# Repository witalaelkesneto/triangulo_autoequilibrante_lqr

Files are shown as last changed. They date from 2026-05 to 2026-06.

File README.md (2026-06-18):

# Triângulo Autoequilibrante com Roda de Reação

Este repositório reúne os códigos, modelos 3D e arquivos auxiliares desenvolvidos para o projeto **Desenvolvimento de um Triângulo Autoequilibrante como Plataforma Didática de Controle**, elaborado como parte do trabalho de conclusão do curso de Engenharia de Controle e Automação.

O projeto consiste no desenvolvimento de uma planta didática baseada em um triângulo autoequilibrante com roda de reação. A proposta tem como objetivo integrar conceitos de modelagem matemática, controle moderno, controle não linear, sistemas embarcados, instrumentação e validação experimental em uma plataforma física de baixo custo.

A planta utiliza uma estrutura fabricada por impressão 3D, um motor de corrente contínua com encoder integrado, um sensor inercial MPU6050, uma roda de reação e um microcontrolador ESP32. O controle é dividido em duas etapas principais: uma estratégia de elevação automática do tipo *swing-up*, baseada no princípio de controle de energia, e um controlador LQR discreto responsável pela estabilização da planta em torno da posição vertical.

## Vídeo do projeto

O vídeo demonstrativo do funcionamento da planta pode ser acessado no link abaixo:

- **Vídeo:** https://youtu.be/2tPs7unF_Ww

## Estrutura do repositório

O repositório contém os principais arquivos utilizados nas etapas de modelagem, simulação, implementação embarcada, coleta de dados, geração dos gráficos experimentais e fabricação da estrutura mecânica.

```text
.
├── Modelo 3D
│   ├── STEP
│   │   ├── CAD Imports
│   │   ├── Assembly 1.step
│   │   ├── Suporte.step
│   │   ├── Triangle_Frame.step
│   │   ├── Triangle_ESP.step
│   │   ├── cubli_motor_holder_3x.step
│   │   └── reaction_wheel.step
│   │
│   └── STL
│       ├── CAD Imports
│       ├── Assembly 1.stl
│       ├── Suporte.stl
│       ├── Triangle_Frame.stl
│       ├── Triangle_ESP.stl
│       ├── cubli_motor_holder_3x.stl
│       └── reaction_wheel.stl
│
├── triangulo_autoequilibrante_lqr.mlx
├── swing_up.mlx
├── triangulo_autoequilibrante_lqr.ino
├── triangulo_autoequilibrante_lqr.py
├── graficos.mlx
└── README.md

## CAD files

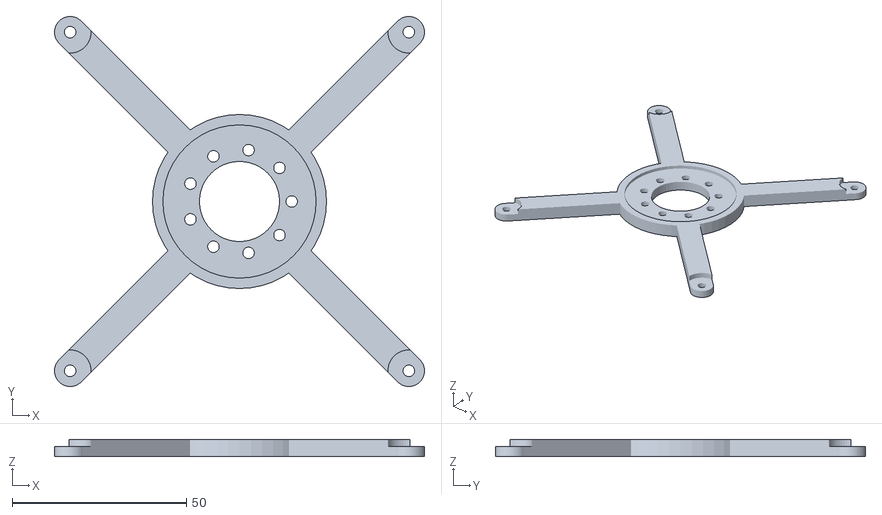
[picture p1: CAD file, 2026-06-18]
Modelo 3D/STEP/CAD Imports/cubli_motor_holder_3x.stl
106.3 x 106.3 x 5.00

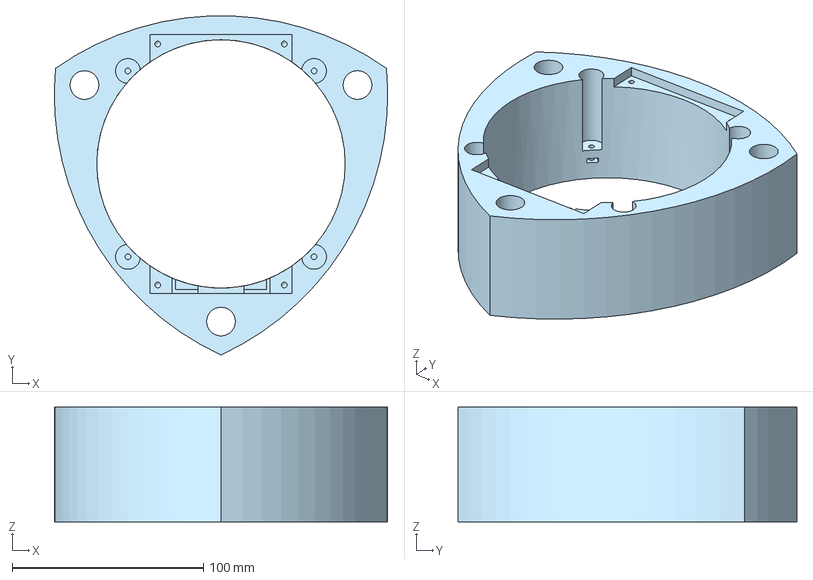
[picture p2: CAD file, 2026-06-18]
Modelo 3D/STEP/Traingle_Frame.step
174.5 x 177.4 x 60.0 mm

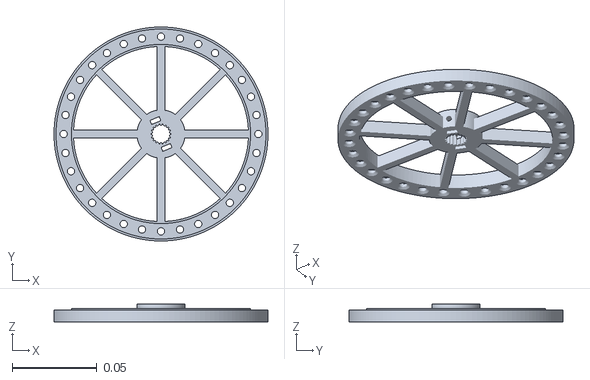
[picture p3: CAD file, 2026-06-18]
Modelo 3D/STL/reaction_wheel.stl
0.126 x 0.126 x 0.0105

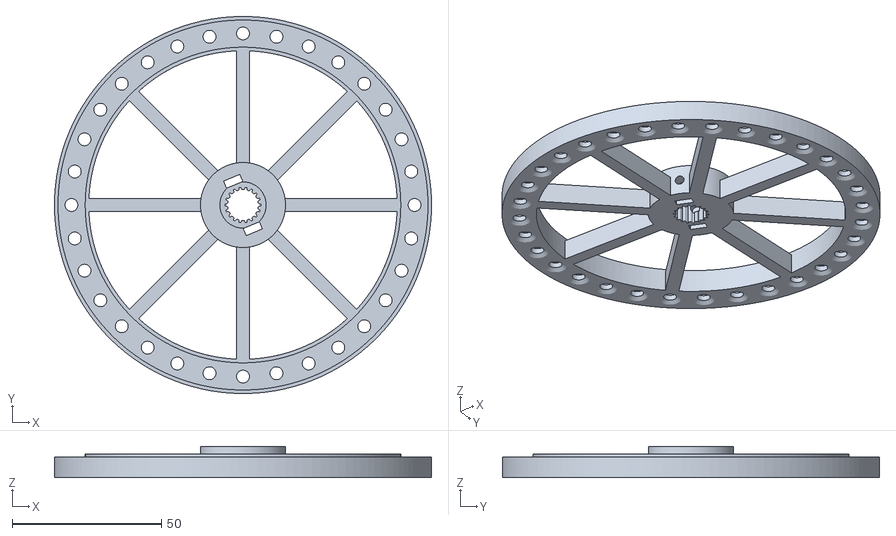
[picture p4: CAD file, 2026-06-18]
Modelo 3D/STEP/CAD Imports/roda-Inercia (2).stl
126.4 x 126.4 x 10.5

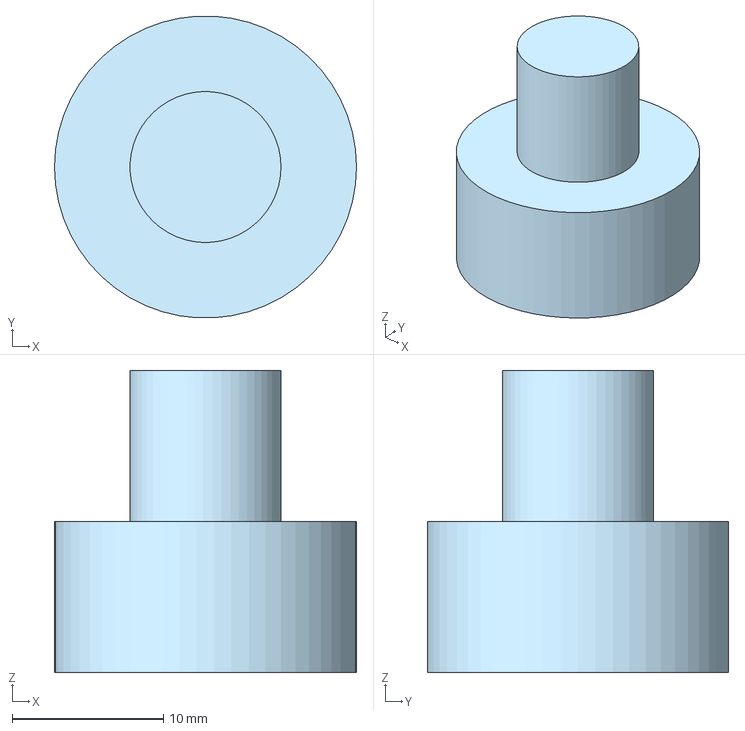
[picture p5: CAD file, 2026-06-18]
Modelo 3D/STEP/Suporte.step
20.0 x 20.0 x 20.0 mm

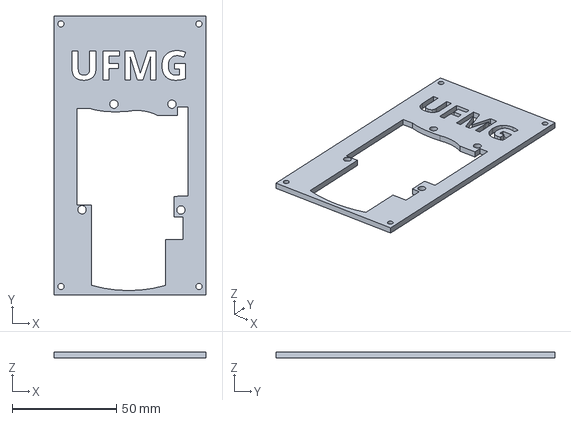
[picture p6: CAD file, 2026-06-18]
Modelo 3D/STEP/Triangle_ESP.step
73.0 x 134.0 x 3.00 mm

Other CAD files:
Modelo 3D/STEP/cubli_motor_holder_3x.step
Modelo 3D/STL/Suporte.stl
Modelo 3D/STL/Traingle_Frame.stl
Modelo 3D/STL/Triangle_ESP.stl
Modelo 3D/STL/cubli_motor_holder_3x.stl

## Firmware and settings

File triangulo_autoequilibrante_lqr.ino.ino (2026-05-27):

/*
  ==========================================================================
   Firmware de controle do triângulo autoequilibrante com roda de reação
  ==========================================================================

  Este código implementa o sistema de controle embarcado da planta utilizada
  no trabalho. O firmware realiza a leitura do sensor inercial MPU6050, estima
  o ângulo da estrutura por meio de um filtro de Kalman, lê o encoder do motor
  da roda de reação, calcula os estados da planta e executa a lógica de controle
  composta pelos modos swing-up, freio e LQR.

  A estratégia de operação é dividida em três modos:
    modo 0: swing-up por energia, utilizado para elevar a planta;
    modo 1: freio, utilizado para reduzir a velocidade angular antes da captura;
    modo 2: LQR, utilizado para estabilizar a planta em torno da posição vertical.

  Durante a execução, o ESP32 envia pela porta serial as principais variáveis
  do ensaio experimental, separadas por vírgula, na seguinte ordem:

    modo, theta, thetaDot, omega, xi, energia, u

  em que:
    modo      -> modo de operação ativo;
    theta     -> ângulo de inclinação da planta [rad];
    thetaDot  -> velocidade angular do corpo [rad/s];
    omega     -> velocidade angular da roda de reação [rad/s];
    xi        -> estado associado à posição acumulada da roda [rad];
    energia   -> energia mecânica calculada [J];
    u         -> tensão equivalente de controle [V].

  Os dados enviados pela serial são coletados posteriormente por um script em
  Python e utilizados na geração dos gráficos experimentais no MATLAB.

  Testado com:
    Arduino IDE 2.3.8
    esp32 package by Espressif Systems 2.0.17

  ==========================================================================
*/

#include <Wire.h>
#include <ESP32Encoder.h>
#include <math.h>

// ===================== PINOS =====================

#define INTERNAL_LED 2

#define MPU_ADDR 0x68

#define PIN_BRAKE 18
#define PIN_PWM 19
#define PIN_DIR 23
#define PIN_ENC_A 5
#define PIN_ENC_B 13

#define PWM_CHANNEL 1
#define PWM_RESOLUTION 8
#define PWM_FREQUENCY 20000

// ===================== ENCODER =====================

ESP32Encoder reactionWheelEncoder;

// ===================== FILTRO DE KALMAN =====================

float Q_angle = 0.001;
float Q_bias  = 0.005;
float R_meas  = 1.0;

float rollAngle = 0.0;
float gyroBias  = 0.0;

float P[2][2] = { { 1, 0 }, { 0, 1 } };
float Kf[2]   = { 0, 0 };

// ===================== AJUSTE DO ÂNGULO =====================

const float ANGLE_OFFSET_DEG = 0.0;
const float ANGLE_POLARITY   = 1.0;

// ===================== GANHOS DO CONTROLADOR LQR =====================

float K1 = -247.9;
float K2 = -26.31;
float K3 = -0.118;
float K4 = 0.011;

// ===================== ESTADOS DA PLANTA =====================

float theta = 0.0;
float thetaDot = 0.0;
float omega = 0.0;
float xi = 0.0;
float xiPrevious = 0.0;

// ===================== SINAL DE CONTROLE =====================

float controlVoltage = 0.0;
int pwmCommand = 0;

// ===================== AMOSTRAGEM =====================

const float Ts = 0.01;
const unsigned long Ts_us = 10000;

unsigned long currentTime = 0;
unsigned long previousTime = 0;

// ===================== CONVERSÕES =====================

const float encoderToRad = 63.7;
const float voltageToPWM = 21.3;

const float maxVoltage = 12.0;
const int maxPWM = 255;

// ===================== PARÂMETROS FÍSICOS DA PLANTA =====================

const float m = 0.498;
const float g = 9.81;
const float l = 0.10;
const float I = 0.00498;

// ===================== CONTROLE SWING-UP POR ENERGIA ====================

const float thetaInicialSwing = 1.0;

const float Einicial = m * g * l * (cos(thetaInicialSwing) - 1.0);

const float Etopo = 0.0;

const float DeltaE = fabs(Einicial - Etopo);

const float excessoEnergia = 0.15;

const float Eref = Etopo + excessoEnergia * DeltaE;

const float kSwing = 0.7*12.2815;

const float polaridadeSwing = -1.0;

const float polaridadeFreio = 1.0;

float energia = 0.0;

// ===================== CRITÉRIOS DE CAPTURA E COMUTAÇÃO =====================

const float thetaLQR = 12.0 / 57.3;
const float thetaDotLQR = 120.0 / 57.3;

const float thetaCaptura = 25.0 / 57.3;

// ===================== MODO DE OPERAÇÃO =====================

int modoControle = 0;

bool lqrAtivo = false;

// ===================== ENVIO SERIAL =====================

int serialCounter = 0;
const int serialDivider = 5;

// ===================== FUNÇÕES AUXILIARES =====================

float normalizeAngle(float angleRad) {
  while (angleRad > PI) {
    angleRad -= 2.0 * PI;
  }

  while (angleRad < -PI) {
    angleRad += 2.0 * PI;
  }

  return angleRad;
}

float signFloat(float value) {
  if (value > 0.0) return 1.0;
  if (value < 0.0) return -1.0;
  return 0.0;
}

// ===================== CONFIGURAÇÃO INICIAL =====================

void setup() {
  Wire.begin();
  Serial.begin(115200);

  pinMode(INTERNAL_LED, OUTPUT);

  setupIMU();
  setupReactionWheelMotor();

  digitalWrite(INTERNAL_LED, HIGH);
  delay(1500);

  for (int i = 0; i < 400; i++) {
    readIMU();
    delay(5);
  }

  reactionWheelEncoder.clearCount();

  theta = 0.0;
  thetaDot = 0.0;
  omega = 0.0;
  xi = 0.0;
  xiPrevious = 0.0;

  controlVoltage = 0.0;
  pwmCommand = 0;

  modoControle = 0;
  lqrAtivo = false;

  previousTime = micros();

  digitalWrite(INTERNAL_LED, LOW);

  Serial.println("Sistema iniciado.");
  Serial.println("modo,theta,thetaDot,omega,xi,energia,u");
}

// ===================== LAÇO PRINCIPAL =====================

void loop() {
  currentTime = micros();

  if ((currentTime - previousTime) >= Ts_us) {
    previousTime += Ts_us;

    readIMU();

    theta = ANGLE_POLARITY * ((rollAngle - ANGLE_OFFSET_DEG) / 57.3);
    theta = normalizeAngle(theta);

    digitalWrite(PIN_BRAKE, HIGH);

    xi = -reactionWheelEncoder.getCount() / encoderToRad;

    omega = -(xi - xiPrevious) / Ts;
    xiPrevious = xi;

    energia = 0.5 * I * thetaDot * thetaDot + m * g * l * (cos(theta) - 1.0);

    if (!lqrAtivo) {
      if ((fabs(theta) < thetaLQR) && (fabs(thetaDot) < thetaDotLQR)) {
        ativarLQR();
      }
    }

    if (lqrAtivo) {
      calcularControleLQR();
      modoControle = 2;
    } else {
      calcularControleSwingOuFreio();
    }

    controlVoltage = constrain(controlVoltage, -maxVoltage, maxVoltage);

    pwmCommand = controlVoltage * voltageToPWM;

    applyMotorCommand(pwmCommand);

    sendSerialData();
  }
}

// ===================== ATIVAÇÃO DO MODO LQR =====================

void ativarLQR() {
  lqrAtivo = true;
  modoControle = 2;

  reactionWheelEncoder.clearCount();

  xi = 0.0;
  xiPrevious = 0.0;
  omega = 0.0;

  controlVoltage = 0.0;
}

// ===================== CONTROLE LQR =====================

void calcularControleLQR() {
  controlVoltage = -(K1 * theta + K2 * thetaDot + K3 * omega + K4 * xi);
}

// ===================== CONTROLE SWING-UP E MODO DE FREIO =====================

void calcularControleSwingOuFreio() {

  if ((fabs(theta) < thetaCaptura) && (fabs(thetaDot) >= thetaDotLQR)) {

    controlVoltage = 0.8*polaridadeFreio * maxVoltage * signFloat(thetaDot);

    controlVoltage = constrain(controlVoltage, -maxVoltage*0.8, maxVoltage*0.8);

    modoControle = 1;

  } else {

    float erroE = energia - Eref;

    float sinal = signFloat(thetaDot);

    controlVoltage = -polaridadeSwing * kSwing * erroE * sinal;

    modoControle = 0;
  }
}

// ===================== CONFIGURAÇÃO DO MPU6050 =====================

void setupIMU() {
  Wire.beginTransmission(MPU_ADDR);
  Wire.write(0x6B);
  Wire.write(0);
  Wire.endTransmission(true);

  Wire.beginTransmission(MPU_ADDR);
  Wire.write(0x1B);
  Wire.write(1 << 3);
  Wire.endTransmission();

  Wire.beginTransmission(MPU_ADDR);
  Wire.write(0x1C);
  Wire.write(0b00000000);
  Wire.endTransmission();
}

// ===================== LEITURA E FILTRAGEM DO MPU6050 =====================

void readIMU() {
  int16_t ax, ay, az, temp, gx, gy, gz;

  Wire.beginTransmission(MPU_ADDR);
  Wire.write(0x3B);
  Wire.endTransmission(false);
  Wire.requestFrom(MPU_ADDR, 14);

  ax = Wire.read() << 8 | Wire.read();
  ay = Wire.read() << 8 | Wire.read();
  az = Wire.read() << 8 | Wire.read();
  temp = Wire.read() << 8 | Wire.read();
  gx = Wire.read() << 8 | Wire.read();
  gy = Wire.read() << 8 | Wire.read();
  gz = Wire.read() << 8 | Wire.read();

  float accelAngle = atan2((float)ay, (float)az) * 57.3;

  float gyroRate = gx / 65.5;

  rollAngle += (gyroRate - gyroBias) * Ts;

  if (rollAngle > 180.0) rollAngle -= 360.0;
  if (rollAngle < -180.0) rollAngle += 360.0;

  P[0][0] += (Q_angle - P[0][1] - P[1][0]) * Ts;
  P[0][1] += -P[1][1] * Ts;
  P[1][0] += -P[1][1] * Ts;
  P[1][1] += Q_bias * Ts;

  Kf[0] = P[0][0] / (P[0][0] + R_meas);
  Kf[1] = P[1][0] / (P[0][0] + R_meas);

  float estimationError = accelAngle - rollAngle;

  if (estimationError > 180.0) estimationError -= 360.0;
  if (estimationError < -180.0) estimationError += 360.0;

  rollAngle += Kf[0] * estimationError;
  gyroBias += Kf[1] * estimationError;

  if (rollAngle > 180.0) rollAngle -= 360.0;
  if (rollAngle < -180.0) rollAngle += 360.0;

  float P00_temp = P[0][0];
  float P01_temp = P[0][1];

  P[0][0] -= Kf[0] * P00_temp;
  P[0][1] -= Kf[0] * P01_temp;
  P[1][0] -= Kf[1] * P00_temp;
  P[1][1] -= Kf[1] * P01_temp;

  thetaDot = ANGLE_POLARITY * ((gyroRate - gyroBias) / 57.3);
}

// ===================== CONFIGURAÇÃO DO MOTOR E DO ENCODER =====================

void setupReactionWheelMotor() {
  pinMode(PIN_BRAKE, OUTPUT);
  pinMode(PIN_DIR, OUTPUT);

  digitalWrite(PIN_BRAKE, HIGH);

  ledcSetup(PWM_CHANNEL, PWM_FREQUENCY, PWM_RESOLUTION);
  ledcAttachPin(PIN_PWM, PWM_CHANNEL);

  applyMotorCommand(0);

  ESP32Encoder::useInternalWeakPullResistors = puType::up;
  reactionWheelEncoder.attachFullQuad(PIN_ENC_B, PIN_ENC_A);
  reactionWheelEncoder.clearCount();
}

// ===================== ACIONAMENTO DO MOTOR =====================

void applyMotorCommand(int command) {
  if (command < 0) {
    digitalWrite(PIN_DIR, HIGH);
    command = -command;
  } else {
    digitalWrite(PIN_DIR, LOW);
  }

  command = constrain(command, 0, maxPWM);

  ledcWrite(PWM_CHANNEL, maxPWM - command);
}

// ===================== TRANSMISSÃO DOS DADOS PELA SERIAL =====================

void sendSerialData() {
  serialCounter++;

  if (serialCounter >= serialDivider) {
    serialCounter = 0;

    Serial.print(modoControle);
    Serial.print(",");
    Serial.print(theta, 6);
    Serial.print(",");
    Serial.print(thetaDot, 6);
    Serial.print(",");
    Serial.print(omega, 6);
    Serial.print(",");
    Serial.print(xi, 6);
    Serial.print(",");
    Serial.print(energia, 6);
    Serial.print(",");
    Serial.println(controlVoltage, 6);
  }
}

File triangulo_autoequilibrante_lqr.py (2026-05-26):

"""
Coleta de dados experimentais do triângulo autoequilibrante via porta serial.

Este script realiza a leitura dos dados enviados pelo ESP32 durante os ensaios
experimentais da planta. O firmware embarcado deve transmitir, em cada linha,
sete valores separados por vírgula, seguindo a ordem:

    modo, theta, theta_dot, omega, xi, energia, u

em que:
    modo      -> modo de operação ativo no firmware
    theta     -> ângulo de inclinação da planta [rad]
    theta_dot -> velocidade angular do corpo [rad/s]
    omega     -> velocidade angular da roda de reação [rad/s]
    xi        -> estado associado à posição acumulada da roda [rad]
    energia   -> energia mecânica calculada [J]
    u         -> tensão equivalente de controle [V]

O programa abre a porta serial configurada, aguarda o recebimento de linhas
numéricas válidas, registra os dados durante o tempo definido em TEMPO_COLETA
e salva as amostras em um arquivo CSV. O nome do arquivo é gerado
automaticamente com data e horário da coleta.

O CSV gerado é utilizado posteriormente no MATLAB para processamento dos dados
experimentais e geração dos gráficos apresentados na monografia.
"""

import serial
import csv
import time
from datetime import datetime


# Configurações da comunicação serial e da coleta

PORTA_SERIAL = "COM3"
BAUDRATE = 115200
TEMPO_COLETA = 40

data_hora = datetime.now().strftime("%Y-%m-%d_%H-%M-%S")
NOME_ARQUIVO = f"dados_planta_{data_hora}.csv"


def linha_numerica_valida(linha):
    """
    Verifica se a linha recebida possui o formato esperado.

    A linha é considerada válida quando contém sete campos separados por
    vírgula e todos podem ser convertidos para valores numéricos.
    """

    dados = linha.split(",")

    if len(dados) != 7:
        return False

    try:
        int(float(dados[0]))
        float(dados[1])
        float(dados[2])
        float(dados[3])
        float(dados[4])
        float(dados[5])
        float(dados[6])
        return True
    except ValueError:
        return False


def tentar_reset_esp32(serial_esp):
    """
    Alterna os sinais DTR e RTS para reiniciar ou liberar a comunicação
    com o ESP32 antes do início da aquisição.
    """

    print("Tentando reiniciar/liberar ESP32...")

    serial_esp.dtr = False
    serial_esp.rts = False
    time.sleep(0.5)

    serial_esp.dtr = True
    serial_esp.rts = True
    time.sleep(0.2)

    serial_esp.dtr = False
    serial_esp.rts = False
    time.sleep(4.5)

    print("ESP32 liberado. Aguardando dados...")


def main():
    print("Iniciando coleta de dados...")
    print(f"Porta: {PORTA_SERIAL}")
    print(f"Baudrate: {BAUDRATE}")
    print(f"Tempo de coleta: {TEMPO_COLETA} s")
    print(f"Arquivo: {NOME_ARQUIVO}")

    try:
        serial_esp = serial.Serial(
            PORTA_SERIAL,
            BAUDRATE,
            timeout=1,
            dsrdtr=False,
            rtscts=False
        )

        tentar_reset_esp32(serial_esp)

        print("Aguardando início dos dados numéricos...")

        with open(NOME_ARQUIVO, mode="w", newline="", encoding="utf-8") as arquivo:
            escritor = csv.writer(arquivo)

            escritor.writerow([
                "tempo_s",
                "modo",
                "theta_rad",
                "theta_dot_rad_s",
                "omega_rad_s",
                "xi_rad",
                "energia_J",
                "u_V"
            ])

            coleta_iniciada = False
            tempo_inicial = None
            tempo_espera = time.time()

            while True:
                linha = serial_esp.readline().decode("utf-8", errors="ignore").strip()

                if not linha:
                    if not coleta_iniciada and (time.time() - tempo_espera > 15):
                        print("\nNenhum dado numérico foi recebido após 15 segundos.")
                        print("Pressione o botão EN/RESET do ESP32 com este programa ainda rodando.")
                        print("Se ainda não aparecer nada, confira se o Monitor Serial da Arduino IDE está fechado.")
                        tempo_espera = time.time()
                    continue

                print(f"Serial: {linha}")

                if not linha_numerica_valida(linha):
                    continue

                if not coleta_iniciada:
                    coleta_iniciada = True
                    tempo_inicial = time.time()
                    print("\nDados numéricos detectados.")
                    print("Coleta iniciada.\n")

                tempo_decorrido = time.time() - tempo_inicial

                if tempo_decorrido >= TEMPO_COLETA:
                    break

                dados = linha.split(",")

                modo = int(float(dados[0]))
                theta = float(dados[1])
                theta_dot = float(dados[2])
                omega = float(dados[3])
                xi = float(dados[4])
                energia = float(dados[5])
                u = float(dados[6])

                escritor.writerow([
                    tempo_decorrido,
                    modo,
                    theta,
                    theta_dot,
                    omega,
                    xi,
                    energia,
                    u
                ])

                print(
                    f"t={tempo_decorrido:.3f}s | "
                    f"modo={modo} | "
                    f"theta={theta:.4f} rad | "
                    f"theta_dot={theta_dot:.4f} rad/s | "
                    f"omega={omega:.4f} rad/s | "
                    f"xi={xi:.4f} rad | "
                    f"E={energia:.4f} J | "
                    f"u={u:.4f} V"
                )

        serial_esp.close()

        print("\nColeta finalizada.")
        print(f"Dados salvos em: {NOME_ARQUIVO}")

    except Exception as e:
        print("Erro ao abrir ou ler a porta serial.")
        print(e)
        print("Verifique se a porta está correta e se o Monitor Serial do Arduino está fechado.")


if __name__ == "__main__":
    main()

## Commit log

2026-05-24 Códigos utilizados no projeto de PFC II
2026-06-18 Adicionando os modelos em 3D
    [Suporte.step, Suporte.stl, Traingle_Frame.step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]
2026-06-18 Alterando o README para indicar a pasta do Modelo 3D
